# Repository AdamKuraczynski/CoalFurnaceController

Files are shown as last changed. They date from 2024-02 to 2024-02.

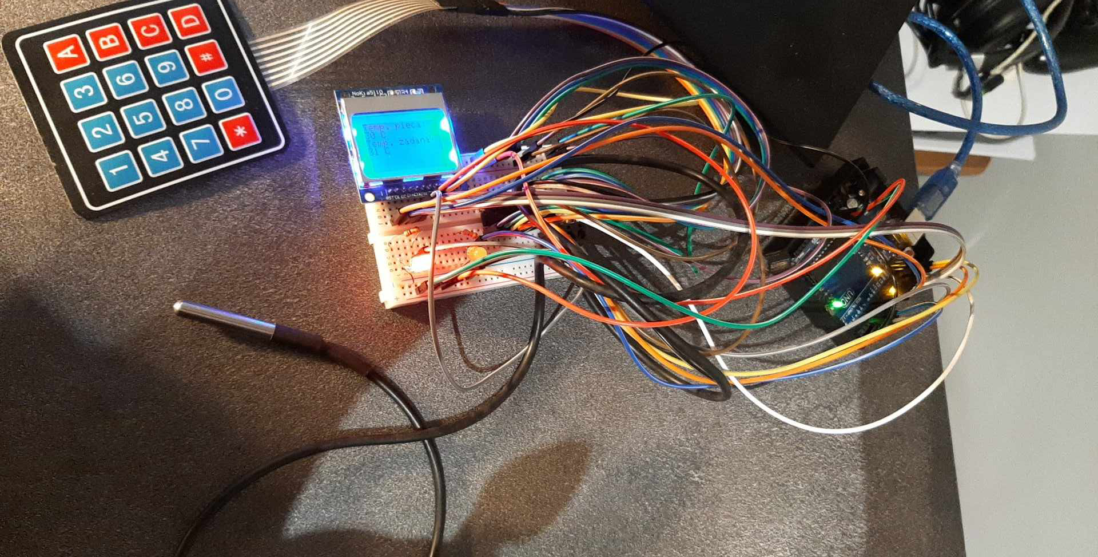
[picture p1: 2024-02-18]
DOC/SPR/IRL Project.png

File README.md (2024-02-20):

# CoalFurnaceController

This project utilizes an Arduino UNO R3 microcontroller as its base to control the pump and blower of a coal furnace. The repository includes all essential files and documents, detailing every step necessary for you to build it yourself.

#### Repository structure:
\PPT - This directory contains the presentation of the project in its initial, intermediate, and final stages. 

\SCH - This directory contains the complete project in Fusion 360 (along with its backup files) with all necessary libraries. It also contains PNG files with schematic and PCB layers.  

\SRC - This directory contains the source code, along with the necessary libraries required for compilation.  

\DOC\SPR - The directory contains all necessary documentation files for the project.  

## Other notes:

##### Hardware:  
Arduino UNO R3  
Breadboard 30  
USB B Cable  
Self-adhesive membrane keyboard 4x4 - 16 keys  
Temperature sensor DS18B20  
Diodes x 2  
Resistors 2x 330 Ohms, 1x 4.7 kOhms  
Pin Expander - Pcf8574 - I2C bus  
84x48 Nokia 5110 3310 display (pcd8544)  

##### Theory:
https://www.elektroda.pl/rtvforum/topic3668747.html   
https://forbot.pl/blog/kurs-elektroniki-prawa-ohma-i-kirchhoffa-id3986  

##### Schematic notes:
Project scanner I2C - checking ports ADDRESS 0x20  
(5-1.7) / 0.01 = 330 Ohms i.e., circuit power - V diode / diode operating range 0.005 to 0.02 = resistor value

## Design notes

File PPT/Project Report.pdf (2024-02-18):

| Instytut Informatyki Politechniki Śląskiej Zespół Mikroinformatyki i Teorii Automatów Cyfrowych
Rok akademicki | Rodzaj studiów*: SSI/NSI/NSM | Przedmiot: (Języki Asemblerowe/SMIW) | Grupa | Sekcja
2023/2024 | NSI | SMIW | 2 | 1
Prowadzący przedmiot: | Dr inż. Gabriel Drabik | | Termin: (dzień tygodnia, godzina)
Imię: Nazwisko: Email: | Adam Kuraczyński ak301824@student.polsl.pl | | Sobota
11:45

## Raport końcowy

Temat projektu:

Sterowanie procesem spalania w piecu węglowym

### Spis treści:

1. Temat projektu, opis założeń, opis funkcji urządzenia
2. Analiza zadania, lista potrzebnych elementów do zbudowania projektu, kosztorys
3. Specyfikacja wewnętrzna urządzenia
1) Schemat blokowy i ideowy urządzenia
2) Opis funkcji poszczególnych bloków układu
3) Schemat montażowy obejmujący projekt płytki drukowanej, rozmieszczenie elementów na płytce
4) Algorytm oprogramowania urządzenia (schemat blokowy)
5) Opis wszystkich zmiennych
6) Opis funkcji procedur
7) Opis integracji oprogramowania z układem elektronicznym
8) Szczegółowy opis działania ważniejszych procedur
4. Specyfikacja zewnętrzna urządzenia
1) Opis funkcji elementów sterujących urządzeniem
2) Opis funkcji elementów wykonawczych
3) Opis reakcji oprogramowania na zdarzenia zewnętrzne
4) Skrócona instrukcja obsługi urządzenia
5. Opis montażu układu, sposobu uruchamiania oraz testowania
1) Problemy, które wystąpiły w trakcie montażu, uruchomienia i ich rozwiązania
2) Testy poprawności działania urządzenia
6. Wnioski końcowe

1. Temat projektu, opis założeń, opis funkcji urządzenia

Tematem projektu jest stworzenie układu zarządzającego sterowaniem piecykiem węglowym starego typu. Taki układ po podłączeniu do prądu powinien mieć możliwość zmiany wartości zadanych w trakcie działania układu oraz wyświetlać aktualnie zadane parametry. Na podstawie zadanych parametrów układ powinien sterować pompą i dmuchawą pieca.

2. Analiza zadania, lista potrzebnych elementów do zbudowania projektu, kosztorys
Wymagane elementy do zbudowania projektu to następująco:
- Zasilanie
- Mikrokontroler
- Wyświetlacz LCD
- Klawiatura
- Czujnik temperatury

Analiza i wybór elementów:
- Mikrokontroler – zdecydowałem się na wybór Arudino Uno R3, gdyż korzystałem już tego urządzenia. Arduino obsługuje prace pod napięciem 5V i pozwala na zasilanie elementów napięciem 3.3V. Obsługuje wymagane I²C, jest kompatybilne z dużą ilością sprzętu i posiada wiele bibliotek.

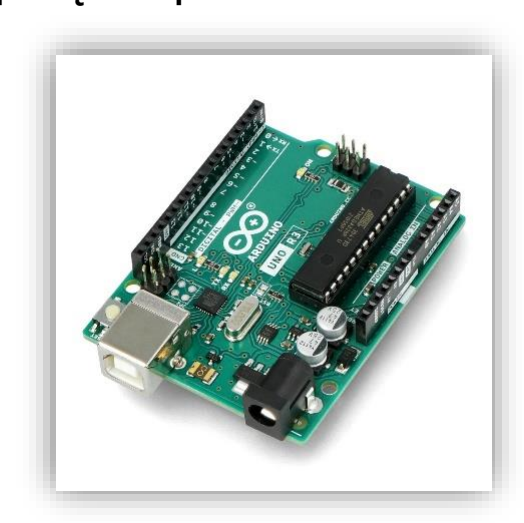
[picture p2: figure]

- Wyświetlacz LCD – zdecydowałem się na 84x48 nokia 5110 3310 (pcd8544). Wyświetlacz jest kompatybilny z Arduino Uno, jest stosunkowo tanim rozwiązaniem, pozwala na wyświetlanie informacji w wielu wierszach co pozwala na wyświetlenie intuicyjnych ekranów. Z powodu prostoty rozwiązania nie zdecydowałem się na wyświetlacz 2x16 HD44780 – nie wprowadza on niczego do projektu. Pracuje pod napięciem 3.3 V co pozwala na podłączenie do Arudino.

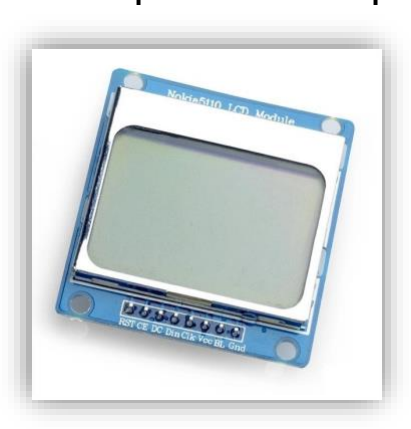
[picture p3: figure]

- Klawiatura – zdecydowałem się na klawiaturę membranowa 4x4 z powodu prostej obsługi z Arduino, dużej ilości
przycisków, | które | będą | potrzebne | do | potencjalnych
dodatkowych funkcjonalności systemu, prostoty działania i niskiego kosztu.

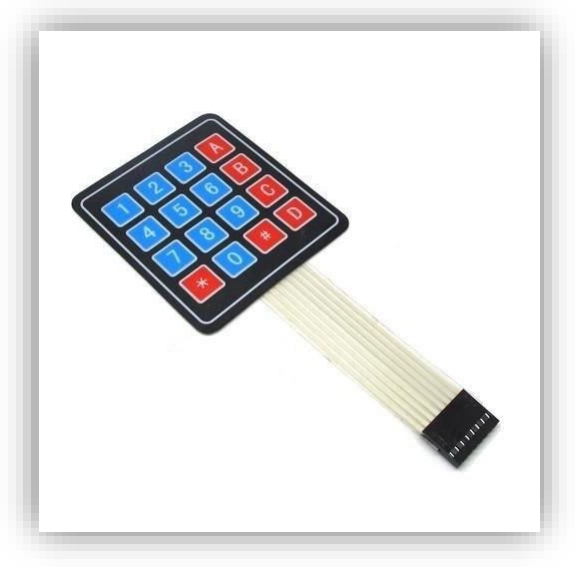
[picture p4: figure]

- Czujnik temperatury – zdecydowałem się na model DS18B20 z powodu bibliotek dostępnych do Arduino, dodatkowego
zabezpieczenia | wodoodpornego, | długiego | kabla
pozwalającego odseparowanie czujnika od reszty elementów, które z pewnością nie chcemy blisko wysokich temperatur.

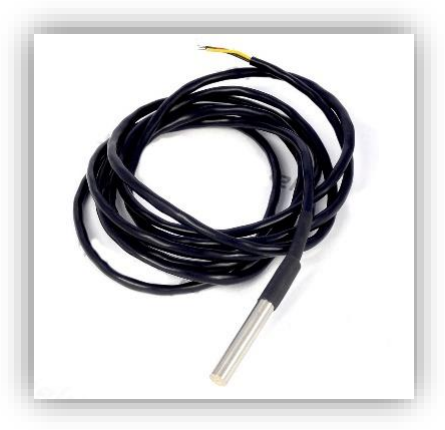
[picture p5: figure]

- Zasilanie układu – zdecydowałem się na zasilanie za pomocą kabla USB typ B z powodu prostej dostępności, możliwości wpięcia do komputera jak i gniazdka używając adaptera. Zasilanie dostarcza wystarczające napięcie do zasilenia Arduino. Jest to również tańsze rozwiązanie w porównaniu do osobnego zasilacza.

Kosztorys:

Rzecz | Sztuk | Koszt
Arduino UNO R3 | 1 | 120
Płytka stykowa 30 | 1 | 7
Kabel USB B | 1 | 20
Klawiatura membranowa samoprzylepna 4x4 - 16 klawiszy | 1 | 5
Czujnik temperatury DS18B20 | 1 | 18
Dioda LED | 2 | 3
Rezystor 330 Om | 2 | 2
Rezystor 4,7k Om | 1 | 2
Ekspander wprowadzeń Pcf8574 | 1 | 15
84 48 Nokia 5110 3310 wyświetlacz (pcd8544) | 1 | 25
Przewody połączeniowe męsko-męskie | 40 | 20
| Suma: | 237

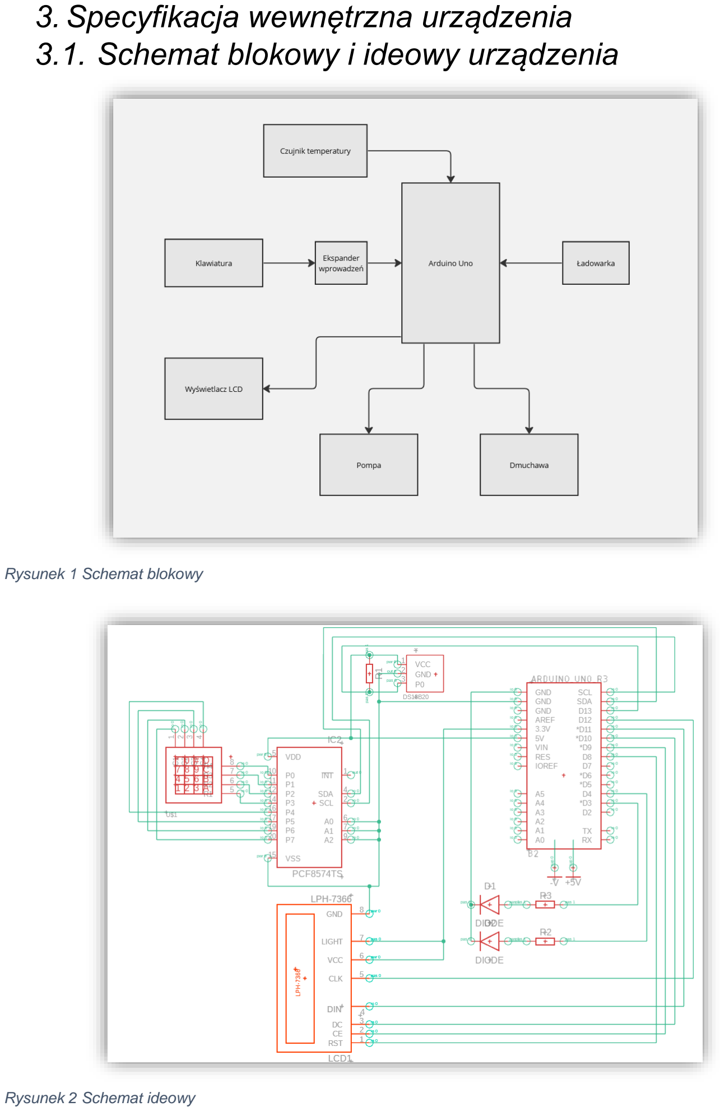
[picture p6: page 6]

3. Specyfikacja wewnętrzna urządzenia
3.1. Schemat blokowy i ideowy urządzenia

Rysunek 1 Schemat blokowy

Rysunek 2 Schemat ideowy

3.2. Opis funkcji poszczególnych bloków układu

Podłączenie klawiatury do ekspandera wprowadzeń – służy do interakcji użytkownika z systemem. Ekspander jest interfejsem w komunikacji klawiatura <-> Arduino.

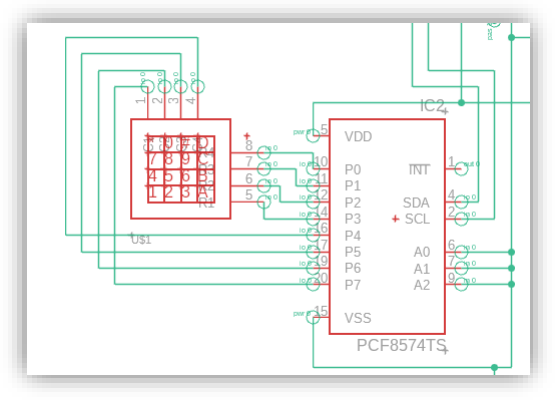
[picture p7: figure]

Podłączenie czujnika temperatury z mikrokontrolerem – służy do stałego odczytu temperatury. Używa protokołu OneWire.

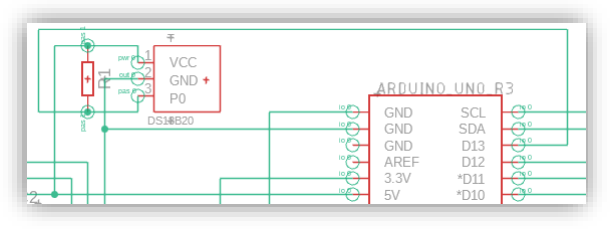
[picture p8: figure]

Podłączenie diod do mikrokontrolera – diody symbolizują pompę i dmuchawę, których włączaniem/wyłączaniem steruje Arduino.

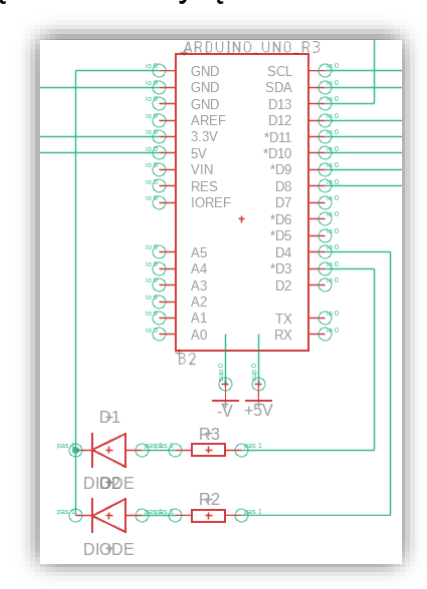
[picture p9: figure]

Podłączenie wyświetlacza – Arduino wysyła dane w celu wyświetlenia ich użytkownikowi. Wyświetlacz używa protokołu SPI.

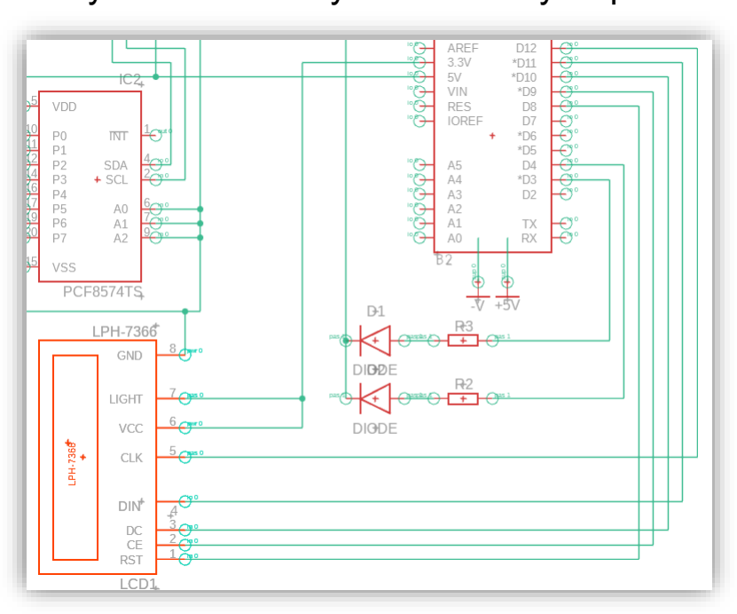
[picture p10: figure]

Podłączenie ekspandera wprowadzeń do mikrokontrolera – ekspander służy jako interfejs między klawiaturą a Arduino, dzięki niemu jest możliwość podpięcia większej ilości pinów cyfrowych. Komunikacja zachodzi przez magistrale I²C.

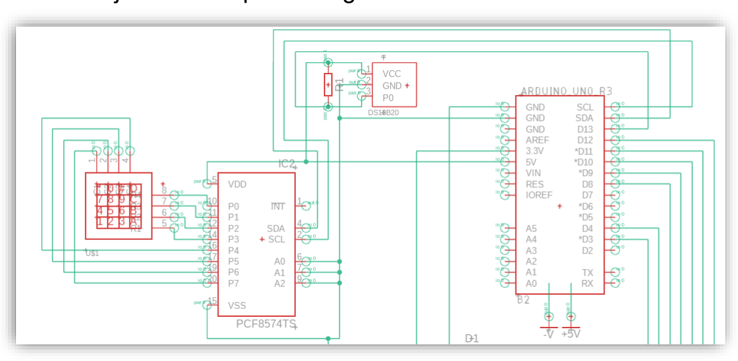
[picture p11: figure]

3.3. Schemat montażowy obejmujący projekt płytki drukowanej, rozmieszczenie elementów na płytce
B2 | ARDUINO _UNO_R3 | ARDUINO_UNO_R3 _SHIELDUNO_R3_S HIELD_NOLABELS_L OCK | UNO_R3_SHIELD_NO LABELS_LOCK | Arduino R3 Shield Footprint
D1 | DIODE | DIODEDO-214AB(SMC) | DIOM7959X625N | Diode Rectifier -Generic | Diode | Rectifier | DIODE
D2 | DIODE | DIODEDO-214AB(SMC) | DIOM7959X625N | Diode Rectifier -Generic | Diode | Rectifier | DIODE
IC2 | PCF8574TS | PCF8574TS | SSOP20 | I2C-Bus Remote 8-bit I/O expander
LCD1 | LPH-7366 | LPH-7366 | LPH-7366
R1 | | R_AXIAL-7.2MM-PITCH | RESAD724W46L381D 178B | Resistor Fixed -Generic | Resistor | Fixed
R2 | | R_AXIAL-7.2MM-PITCH | RESAD724W46L381D 178B | Resistor Fixed -Generic | Resistor | Fixed
R3 | | R_AXIAL-7.2MM-PITCH | RESAD724W46L381D 178B | Resistor Fixed - Generic Resistor | | Fixed
T | DS18B20 | A1324LLHLT-TLH | SOT95P285X113-3N | SENSOR HALL EFFECT ANALOG SOT23W | Sensor | Magnetic | A1324 LLHLT
U$1 | | KEYPAD4X4 | KEYPAD4X4

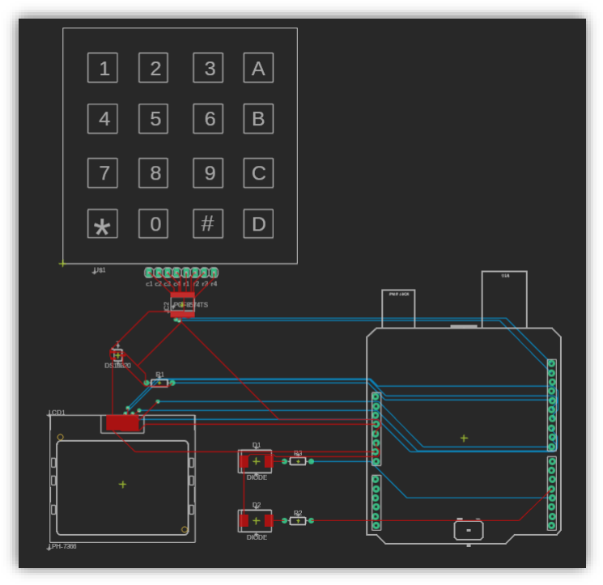
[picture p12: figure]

Rysunek 3 Projekt Płytki

3.4. Algorytm oprogramowania urządzenia (schemat blokowy)

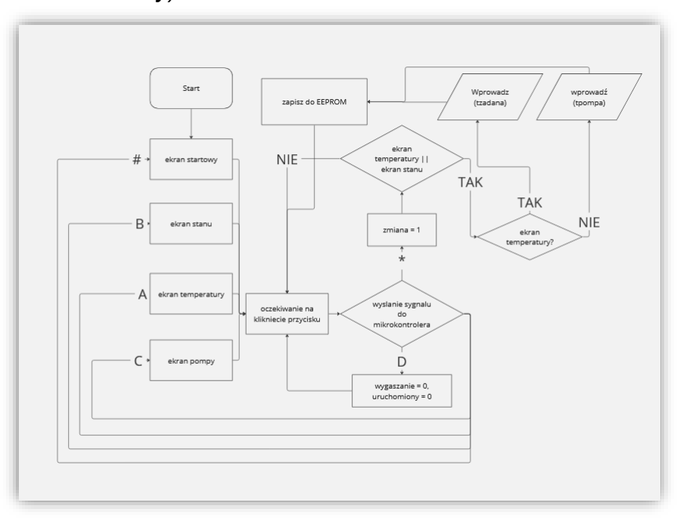
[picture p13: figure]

Rysunek 4 Algorytm blokowy

3.5. Opis wszystkich zmiennych
#define ONE_WIRE_BUS 13 | - zmienna z adresem czujnika temperatury

OneWire oneWire(ONE_WIRE_BUS); | - zmienna tworzaca komunikacje OneWire
DallasTemperature sensors(&oneWire); | - zmienna tworzaca komunikacje DallasTemperature uzywając OneWire
Adafruit_PCD8544 display =
Adafruit_PCD8544(12, 11, 10, 9, 8); | - zmienna tworząca komunikacje z wyswietlaczem
const byte pompa = 3; | - zmienna z adresem pompy
const byte dmuchawa = 4; | - zmienna z adresem dmuchawy
int tzadana = 29; | - zmienna z wartością, do której działa dmuchawa
int tpompa = 27; | - zmienna z wartością temperatury, od której właczana jest pompa
int temperatura; | - zmienna z wartością aktualnej temperatury

byte ekran = 0; | - zmienna pomocnicza do przejść między ekranami
byte zmiana = 0; | - zmienna sygnalizujaca wejście do Trybu Edycji
byte uruchomiony=0; | - zmienna sygnalizujaca uruchomienie Pompy
byte wygaszanie=0; | - zmienna sygnalizująca skończenie 1 cyklu działania układu
const byte ROWS = 4; | - zmienna pomocnicza z ilościa wierszy
const byte COLS = 4; | - zmienna pomocnicza z ilościa kolumn
Char keys[ROWS][COLS] = {
{'1','2','3','A'},
{'4','5','6','B'},
{'7','8','9','C'},
{'*','0','#','D'} };
- zmienna pomocnicza mapująca wartości klawiszy
byte rowPins[ROWS] = {0, 1, 2, 3}; | - zmienna pomocnicza z adresami wierszy klawiatury
byte colPins[COLS] = {4, 5, 6, 7}; | - zmienna pomocnicza z adresami kolumn klawiatury
int i2caddress = 0x20; | - zmienna pomocnicza z adresem i2c ekspandera wprowadzeń
Keypad_I2C kpd = Keypad_I2C(
makeKeymap(keys), rowPins, colPins,
ROWS, COLS, i2caddress );
- zmienna tworząca komunikacje klawiatury

temperatura=sensors.getTempCByIndex(0); - zmienna do przechowywania temperatury odebranej przes czujnik
char klawisz = kpd.getKey(); | - zmienna do przechowywania ostatniego wciśniętego przycisku
3.6. Opis funkcji procedur
int odczytLiczba() | - funkcja, która zwraca zmieniona wartość temperatury
int odczytCyfra() | - funkcja, która odczytuje cyfry z klawiatury w celu zmiany temperatury zadanej
void EkranStartowy() | - funkcja inicjująca ekran startowy
void EkranTemperatury () | - funkcja inicjująca ekran temperatury
void EkranStanu() | - funkcja inicjująca ekran stanu
void EkranPompa() | - funkcja inicjująca ekran pompy
void setup() | - funkcja ustawiająca interfejsy do obsługi
void loop() | - główna funkcja mikrokontrolera, zarządza zmianami ekranów i zachowaniem pompy i dmuchawy
switch (klawisz) | - przełącznik obsługujący zmiane ekranów
switch (ekran) | - przełącznik obsługujący zmiane ekranów
display.clearDisplay(); | - czyści ekran
display.setTextSize(1); | - zmienia wielkość czcionki na ekranie
display.setTextColor(BLACK); | - zmienia kolor czcionki na ekranie
display.setCursor(0, 0); | - ustawia pozycje kursora

display.print(); | - drukuje tekst do ekranu
display.println(); | - przechodzi do nowej linii na ekranie
display.display(); | - wyświetla cały kontekst na ekranie
display.begin(); | - inicializuje ekran
display.setContrast(60); | - zmienia kontrast ekranu
Serial.begin(9600); | - rozpoczyna komunikacje seryjną
sensors.begin(); | - inicializuje czujniki temperatury
Wire.begin(); | - inicializuje komunikacje I2C
kpd.begin(); | - inicializuje klawiature
pinMode(pompa, OUTPUT); | - konfiguruje pin jako wyjście
pinMode(dmuchawa, OUTPUT); - konfiguruje pin jako wyjście
EEPROM.put(100, tzadana); | - wpisuje wartość tzadana do EEPROM na adresie 100
EEPROM.get(100, tzadana); | - odczytuje wartość tzadana z EEPROM z adresu 100
sensors.requestTemperatures(); - inicialuzje pomiary temperatury z sensora temperatury
sensors.getTempCByIndex(i); | - odczytuje wartość temperatury z sensora
digitalWrite(dmuchawa,HIGH); | - ustawia pin dmuchawa jako 1
digitalWrite(dmuchawa,LOW); | - ustawia pin dmuchawa jako 0
digitalWrite(pompa,HIGH); | - ustawia pin pompa jako 1
digitalWrite(pompa,LOW); | - ustawia pin pompa jako 0
3.7. Opis | integracji | oprogramowania | z | układem
elektronicznym

Oprogramowanie wykorzystuje następne biblioteki:

- Adafruit_GFX oraz Adafruit_PCD8544 – wykorzystane w celu zapewnienia komunikacji z wyświetlaczem NOKIA typu PCD8544,
- Keypad_I2C - wykorzystana do zapewnienia komunikacji z klawiaturą, użyta została Keypad_I2C a nie Keypad jako że komunikacja zachodzi poprzez ekspander wprowadzeń I2C,
- Wire, OneWire, DallasTemperature - wykorzystane, aby zapewnić komunikację z czujnikiem temperatury,
- EEPROM - wykorzystana, aby wartości zadane dla pompy oraz dmuchawy były zachowane między włączeniami systemu.

3.8. Szczegółowy opis działania ważniejszych procedur

Gdy aktualnie odczytana temperatura jest wyższa niż zadana dla systemu oraz jego tryb to wygaszanie to dmuchawa jest wyłączona. Jeśli nie to dmuchawa działa, jest to zabezpieczenie przed działaniem dmuchawy cały czas

if ((temperatura>=tzadana)||(wygaszanie==1)) digitalWrite(dmuchawa,LOW);
else digitalWrite(dmuchawa,HIGH);

Gdy aktualnie odczytana temperatura jest wyższa od temperatury zadanej dla pompy to pompa się uruchamia, a system przechodzi w tryb uruchomiony tj. grzeje dom.

if(temperatura>tpompa) {
digitalWrite(pompa,HIGH);
uruchomiony=1;
} else digitalWrite(pompa,LOW);

Gdy cykl został uruchomiony tj. pompa choć raz się włączyła oraz aktualny stan pompy to 0, czyli wyłączona to rozpoczyna się proces wygaszania mający na celu zabezpieczenie systemu przed działaniem dmuchawy cały czas.

if((uruchomiony==1)&&(digitalRead(pompa)==0)) wygaszanie=1;

Zawsze pierwsza liczba wprowadzona w Trybie edycji to liczba dziesiątek a druga liczba jedności.

int odczytLiczba()
{
return odczytCyfra() * 10 + odczytCyfra(); }

4. Specyfikacja zewnętrzna urządzenia
4.1. Opis funkcji elementów sterujących urządzeniem

Sterowanie używając klawiatury:

- Przycisk „A” – przejście do Ekranu Temperatury
- Przycisk „B” – przejście do Ekranu Stanu
- Przycisk „C” – przejście do Ekranu Pompy
- Przycisk „#” – przejście do Ekranu Startowego
- Przycisk „D” – zresetowanie zmiennych i ponowne uruchomienie cyklu
- Przycisk „*” – przejście do Trybu Edycji temperatury na Ekranie Temperatury i Ekranie Pompy
- Przyciski 0-9 – w Trybie Edycji pozwalają na wybranie temperatury

Układ jest wyposażony w przycisk restartu pozwalający na restart mikrokontrolera.

4.2. Opis funkcji elementów wykonawczych

84 48 Nokia 5110 3310 Wyświetlacz LED (pcd8544) – wyświetla informacje o temperaturze i stanach pompy i dmuchawy oraz zadanych wartościach
Dioda czerwona – symbolizuje uruchomienie pompy pieca węglowego Dioda żółta – symbolizuje uruchomienie dmuchawy pieca węglowego Czujnik temperatury DS18B20 – odczytuje temperaturę

4.3. Opis | reakcji | oprogramowania | na | zdarzenia
zewnętrzne

Wciśnięcie przycisku „A” – przejście do Ekranu Temperatury Wciśnięcie przycisku „B” – przejście do Ekranu Stanu Wciśnięcie przycisku „C” – przejście do Ekranu Pompy Wciśnięcie przycisku „#” – przejście do Ekranu Startowego Wciśnięcie przycisku „D” – zresetowanie zmiennych i ponowne uruchomienie cyklu
Wciśnięcie przycisku „*” – przejście do Trybu Edycji temperatury na Ekranie Temperatury i Ekranie Pompy
Wciśnięcie przycisków 0-9 – w Trybie Edycji pozwalają na wybranie temperatury
Wciśnięcie przycisku restartu na mikrokontrolerze – resetuje mikrokontroler a ekran wraca do Ekranu Startowego
Podłączenie i odłączenie źródła zasilania – uruchamia i wyłącza urządzenie
Czujnik temperatury – ogrzanie lub oziębienie czujnika zmienia działanie całego układu - włącza bądź wyłącza pompę i dmuchawę
4.4. Skrócona instrukcja obsługi urządzenia

Po podłączeniu urządzenia do prądu na wyświetlaczu pojawia się ekran startowy. Informuje nas o tym, że klikając na klawiaturze „A” przenosimy się do Ekranu Temperatury, klikając „B” do Ekranu Stanu a klikając „C” do Ekranu Pompy. Klikając „#” wracamy do ekranu startowego. Na ekranie temperatury otrzymujemy informacje o temperaturze pieca tj. aktualnej temperaturze zmierzonej przez czujnik temperatury oraz temperaturze zadanej to jest temperatury, która chcemy osiągnąć – temperatura, do której ma być uruchomiona dmuchawa. Ekran Stanu informuje nas o aktualnym stanie dmuchawy i pompy, czy są włączone czy nie.

Ekran Pompy informuje nas o temperaturze włączenia pompy. Klikając „*” na klawiaturze na Ekranie Temperatury jesteśmy w stanie zmienić zadana temperaturę dmuchawy, a na ekranie Pompy klikając „*” na klawiaturze jesteśmy w stanie zmienić temperaturę zadana pompy. Po zadaniu tych temperatur w standardowym przypadku dmuchawa powinna się włączyć, po tym pompa powinna się włączyć, następnie wyłącza się dmuchawa, a po tym pompa – dochodzi do resetu systemu. Po tym wystarczy, że na klawiaturze wciśniemy „D” aby zresetować system – dmuchawa znowu zacznie działać. To zabezpiecza system przed działaniem cały czas – nawet jak tego nie chcemy.

5. Opis montażu układu, sposobu uruchamiania oraz testowania

Układ został podłączony używając płytki prototypowej. Na płytce umieszczone zostały diody, rezystory, wyświetlacz, czujnik temperatury oraz ekspander wprowadzeń. Następnie używając przewodów połączeniowych wszystko zostało ze sobą połączone i osobno przetestowane w kolejności czujnik temperatury, diody i rezystory, wyświetlacz, klawiatura i ekspander wprowadzeń. Po podłączeniu wszystkiego wykonane zostało oprogramowanie, które testuje każde z urządzeń.

5.1. Problemy, które wystąpiły w trakcie montażu, uruchomienia i ich rozwiązania

W trakcie testowania urządzenia z przyczyn mi nieznanych wyświetlacz LCD przestał działać, zmuszony byłem do zakupu nowego egzemplarza.

5.2. Testy poprawności działania urządzenia

Testy opierały się na sprawdzeniu pełnej funkcjonalności urządzenia: działanie klawiatury, wyświetlacza, bieżący pomiar temperatury, jak reagują pompa i dmuchawa na odmierzone temperatury oraz czy układ działa po podłączeniu do zasilania. Wszystkie testy przeszły pomyślnie.

6. Wnioski końcowe

Układ sprawdza się, jeśli chodzi o podstawowe wymogi. Można jednak go rozbudować o dodatkowe funkcjonalności:

- Zamknąć go w obudowie, aby zabezpieczyć elementy,
- Odczytanie temperatury mogłoby zostać wykonywane w części mieszkalnej budynku a informacja o temperaturze przekazywana do głównego kontrolera,
- Można | usprawnić | wyświetlanie | komunikatów | na
wyświetlaczu, aby wszystko odbywało się na jednej stronie bez wymogu zmiany ekranów wyświetlania.

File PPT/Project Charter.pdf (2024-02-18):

Data | Ocena:

Założenia:

Prezentacja:

Implementacja

Raport

Ocena końcowa:

Data | Obecność | Uwagi
| Instytut Informatyki Politechniki Śląskiej Zespół Mikroinformatyki i Teorii Automatów Cyfrowych
Rok akademicki | Rodzaj studiów*: SSI/NSI/NSM | Przedmiot: (Języki Asemblerowe/SMIW) | Grupa | Sekcja
2023/2024 | NSI | SMIW | 2 | 1
Prowadzący przedmiot: | Dr inż. Gabriel Drabik | | Termin: (dzień tygodnia, godzina)
Imię: Nazwisko: Email: | Adam Kuraczyński ak301824@student.polsl.pl | | Sobota
11:45

## Karta projektu

Temat projektu:

Sterowanie procesem spalania w piecu węglowym

Główne założenia projektu:
Układ ma na celu zautomatyzowanie procesu spalania w piecyku węglowym starego typu. Do płytki Arduino UNO R3 podłączone są następujące elementy: wyświetlacz graficzny 84x48 LCD NOKIA 5110/3310, czujnik temperatury, klawiatura membranowa 4x4, dmuchawa i pompa pieca (ich podpięcie zasymuluje poprzez użycie diod). Z powodu braku wystarczającej ilości pinów na płytce do podpięcia klawiatury użyty zostanie ekspander wprowadzeń magistrali I2C 8-bitowy Pcf8574.

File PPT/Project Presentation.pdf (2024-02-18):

## Sterowanie procesem spalania w piecu węglowym

Adam Kuraczyński

# Założenie

- Umożliwienie sterowania procesu spalania w piecyku
węglowym starego typu
- Możliwość zmiany wartości zadanych w trakcie działania układu – bez potrzeby jego wyłączania

# Elementy układu

- Moduł Arduino UNO R3,
- Wyświetlacz graficzny 84x48 LCD NOKIA 5110/3310,
- Czujnik temperatury DS18B20,
- Klawiatura membranowa 4x4,
- Dmuchawa i pompa pieca (ich podpięcie zasymuluje poprzez użycie żółtej i czerwonej diody)
- Ekspander wyprowadzeń I²C 8-bitowy PCF8574,
- Rezystor 4.6 kΩ,
- Rezystor 330 Ω x 2,

# Sposób działania

- Sterowanie układem przez użytkownika zachodzi poprzez interfejs I²C
- Komunikacja z wyświetlaczem odbywa się poprzez interfejs SPI (Serial Peripheral Interface)
- Status pracy urządzenia, odczytane wartości oraz informacje zwrotne wyświetlane są na ekranie LCD
- Układ zasilany jest napięciem 5V (USB 2.0)

# Schemat ideowy układu

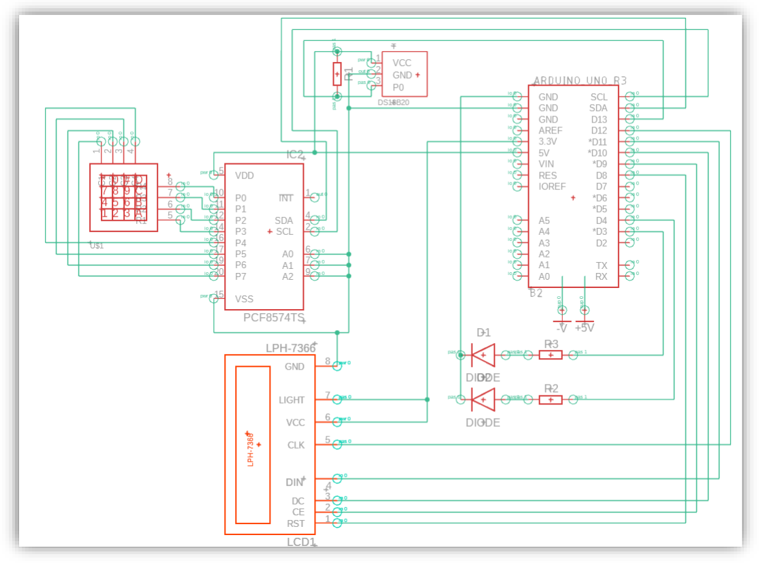
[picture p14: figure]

# Aktualny stan prac

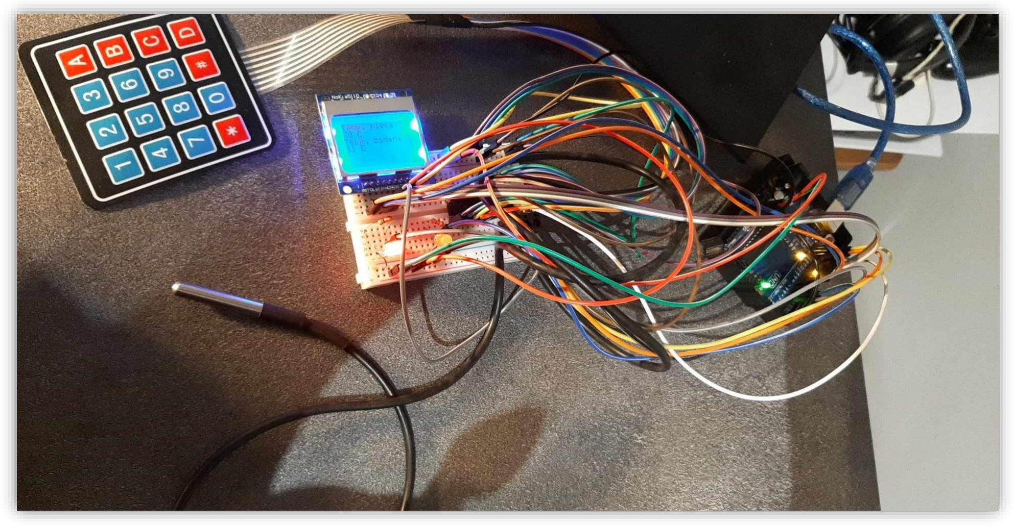
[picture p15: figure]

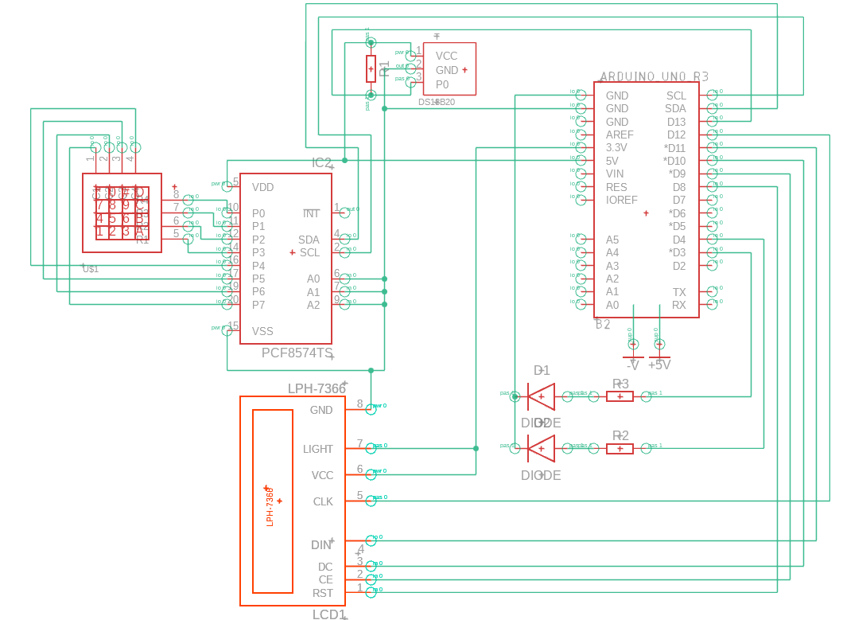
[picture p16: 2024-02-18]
SCH/Circuit Schematic.png

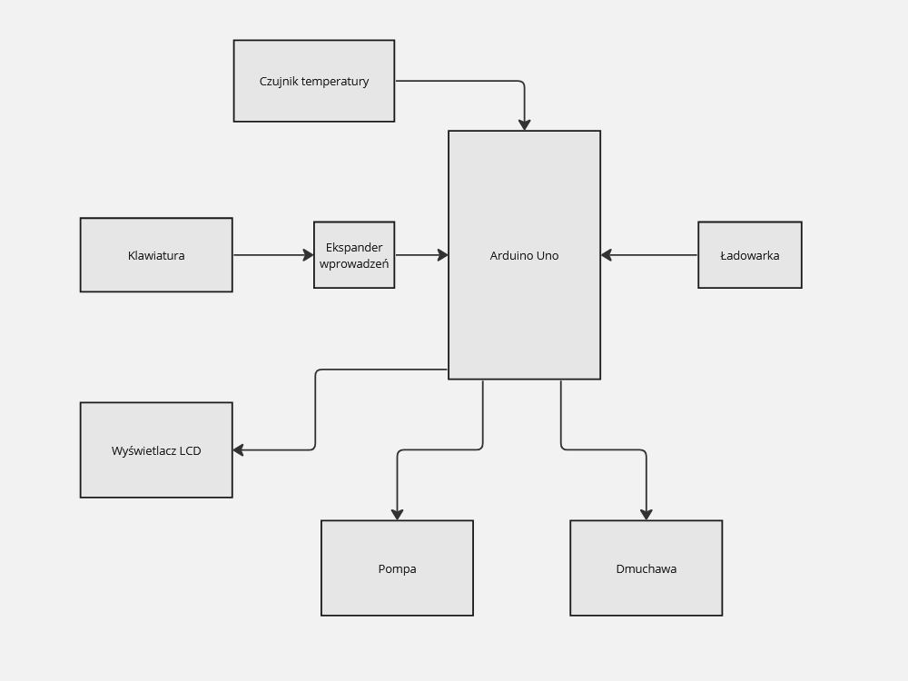
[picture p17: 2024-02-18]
DOC/SPR/Block Diagram.png

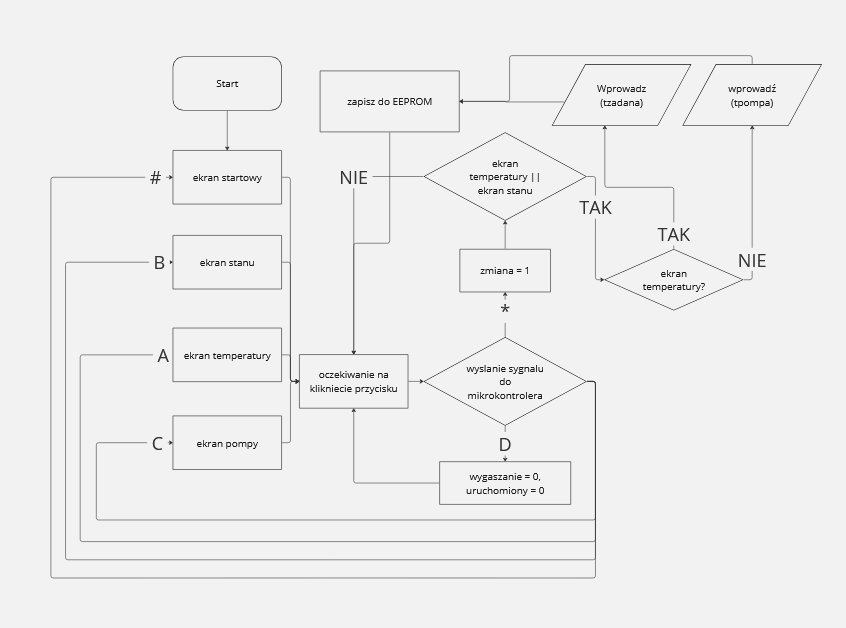
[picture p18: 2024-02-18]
DOC/SPR/Algorithm Block Diagram.png

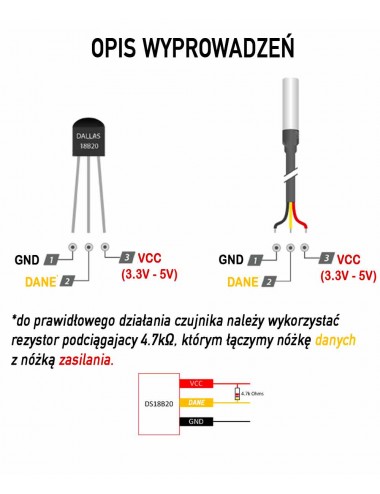
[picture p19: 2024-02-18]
DOC/SPR/TemperatureSensorDS18B20.png

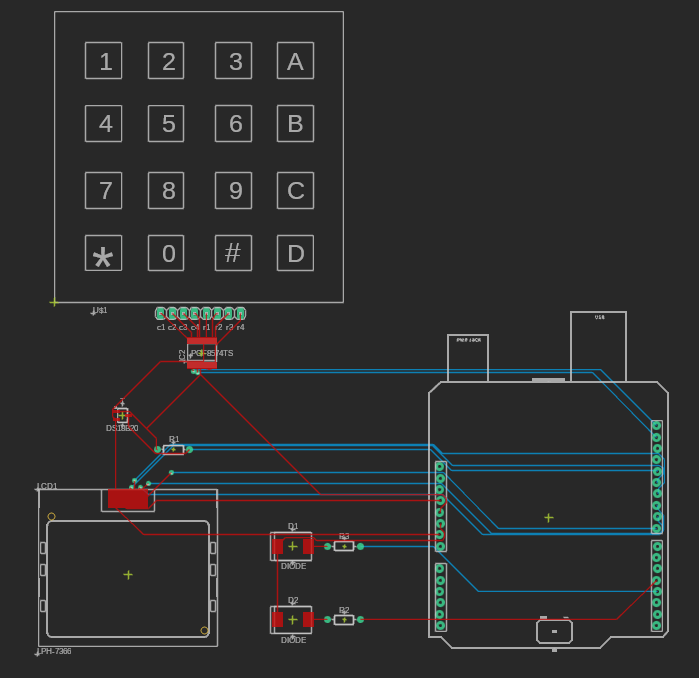
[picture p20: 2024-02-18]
SCH/PCB Board.png

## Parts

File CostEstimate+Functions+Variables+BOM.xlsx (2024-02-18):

#define ONE_WIRE_BUS 13 | - | zmienna z adresem czujnika temperatury | Rzecz | Sztuk | Koszt | Part | Value | Device | Package | Description | CAT | SUB-CAT | VALUE
OneWire oneWire(ONE_WIRE_BUS); | - | zmienna tworzaca komunikacje OneWire | Arduino UNO R3 | 1 | 120 | B2 | ARDUINO_UNO_R3 | ARDUINO_UNO_R3_SHIELDUNO_R3_SHIELD_NOLABELS_LOCK | UNO_R3_SHIELD_NOLABELS_LOCK | Arduino R3 Shield Footprint
DallasTemperature sensors(&oneWire); | - | zmienna tworzaca komunikacje DallasTemperature uzywając OneWire | Płytka stykowa 30 | 1 | 7 | D1 | DIODE | DIODEDO-214AB(SMC) | DIOM7959X625N | Diode Rectifier - Generic | Diode | Rectifier | DIODE
Adafruit_PCD8544 display = Adafruit_PCD8544(12, 11, 10, 9, 8); | - | zmienna tworząca komunikacje z wyswietlaczem | Kabel USB B | 1 | 20 | D2 | DIODE | DIODEDO-214AB(SMC) | DIOM7959X625N | Diode Rectifier - Generic | Diode | Rectifier | DIODE
const byte pompa = 3; | - | zmienna z adresem pompy | Klawiatura membranowa samoprzylepna 4x4 - 16 klawiszy | 1 | 5 | IC2 | PCF8574TS | PCF8574TS | SSOP20 | I2C-Bus Remote 8-bit I/O expander
const byte dmuchawa = 4; | - | zmienna z adresem dmuchawy | Czujnik temperatury DS18B20 | 1 | 18 | LCD1 | LPH-7366 | LPH-7366 | LPH-7366
int tzadana = 29; | - | zmienna z wartością do której działa dmuchawa | Dioda LED | 2 | 3 | R1 |  | R_AXIAL-7.2MM-PITCH | RESAD724W46L381D178B | Resistor Fixed - Generic | Resistor | Fixed
int tpompa = 27; | - | zmienna z wartością temperatury od której właczana jest pompa | Rezystor 330 Om | 2 | 2 | R2 |  | R_AXIAL-7.2MM-PITCH | RESAD724W46L381D178B | Resistor Fixed - Generic | Resistor | Fixed
int temperatura; | - | zmienna z wartością aktualnej temperatury | Rezystor 4,7k Om | 1 | 2 | R3 |  | R_AXIAL-7.2MM-PITCH | RESAD724W46L381D178B | Resistor Fixed - Generic | Resistor | Fixed
byte ekran = 0; | - | zmienna pomocnicza do przejść między ekranami | Ekspander wprowadzeń Pcf8574 | 1 | 15 | T | DS18B20 | A1324LLHLT-TLH | SOT95P285X113-3N | SENSOR HALL EFFECT ANALOG SOT23W | Sensor | Magnetic | A1324LLHLT
byte zmiana = 0; | - | zmienna sygnalizujaca wejście do Trybu Edycji | 84 48 Nokia 5110 3310 wyświetlacz (pcd8544) | 1 | 25 | U$1 |  | KEYPAD4X4 | KEYPAD4X4
byte uruchomiony=0; | - | zmienna sygnalizujaca uruchomienie Pompy | Przewody połączeniowe męsko-męskie | 40 | 20
byte wygaszanie=0; | - | zmienna sygnalizująca skończenie 1 cyklu działania układu |  | Suma: | 237
const byte ROWS = 4; | - | zmienna pomocnicza z ilościa wierszy
const byte COLS = 4; | - | zmienna pomocnicza z ilościa kolumn
char keys[ROWS][COLS] = { {'1', '2', '3', 'A'}, {'4', '5', '6', 'B'}, {'7', '8', '9', 'C'}, {'*', '0', '#', 'D'} }; | - | zmienna pomocnicza mapująca wartości klawiszy
byte rowPins[ROWS] = {0, 1, 2, 3}; | - | zmienna pomocnicza z adresami wierszy klawiatury
byte colPins[COLS] = {4, 5, 6, 7}; | - | zmienna pomocnicza z adresami kolumn klawiatury
int i2caddress = 0x20; | - | zmienna pomocnicza z adresem i2c ekspandera wprowadzeń
Keypad_I2C kpd = Keypad_I2C( makeKeymap(keys), rowPins, colPins, ROWS, COLS, i2caddress ); | - | zmienna tworząca komunikacje klawiatury
temperatura=sensors.getTempCByIndex(0); | - | zmienna do przechowywania temperatury odebranej przes czujnik
char klawisz = kpd.getKey(); | - | zmienna do przechowywania ostatniego wciśniętego przycisku
int odczytLiczba() | - | funkcja która zwraca zmieniona wartość temperatury
int odczytCyfra() | - | funkcja która odczytuje cyfry z klawiatury w celu zmiany temperatury zadanej
void EkranStartowy() | - | funkcja inicjująca ekran startowy
void EkranTemperatury () | - | funkcja inicjująca ekran temperatury
void EkranStanu() | - | funkcja inicjująca ekran stanu
void EkranPompa() | - | funkcja inicjująca ekran pompy
void setup() | - | funkcja ustawiająca interfejsy do obsługi
void loop() | - | główna funkcja mikrokontrolera, zarządza zmianami ekranów i zachowaniem pompy i dmuchawy
switch (klawisz) | - | przełącznik obsługujący zmiane ekranów
switch (ekran) | - | przełącznik obsługujący zmiane ekranów
display.clearDisplay(); | - | czyści ekran
display.setTextSize(1); | - | zmienia wielkość czcionki na ekranie
display.setTextColor(BLACK); | - | zmienia kolor czcionki na ekranie
display.setCursor(0, 0); | - | ustawia pozycje kursora
display.print(); | - | drukuje tekst do ekranu
display.println(); | - | przechodzi do nowej linii na ekranie
display.display(); | - | wyświetla cały kontekst na ekranie
display.begin(); | - | inicializuje ekran
display.setContrast(60); | - | zmienia kontrast ekranu
Serial.begin(9600); | - | rozpoczyna komunikacje seryjną
sensors.begin(); | - | inicializuje czujniki temperatury
Wire.begin(); | - | inicializuje komunikacje I2C
kpd.begin(); | - | inicializuje klawiature
pinMode(pompa, OUTPUT); | - | konfiguruje pin jako wyjście
pinMode(dmuchawa, OUTPUT); | - | konfiguruje pin jako wyjście
EEPROM.put(100, tzadana); | - | wpisuje wartość tzadana do EEPROM na adresie 100
EEPROM.get(100, tzadana); | - | odczytuje wartość tzadana z EEPROM z adresu 100
sensors.requestTemperatures(); | - | inicialuzje pomiary temperatury z sensora temperatury
sensors.getTempCByIndex(i); | - | odczytuje wartość temperatury z sensora
digitalWrite(dmuchawa,HIGH); | - | ustawia pin dmuchawa jako 1
digitalWrite(dmuchawa,LOW); | - | ustawia pin dmuchawa jako 0
digitalWrite(pompa,HIGH); | - | ustawia pin pompa jako 1
digitalWrite(pompa,LOW); | - | ustawia pin pompa jako 0

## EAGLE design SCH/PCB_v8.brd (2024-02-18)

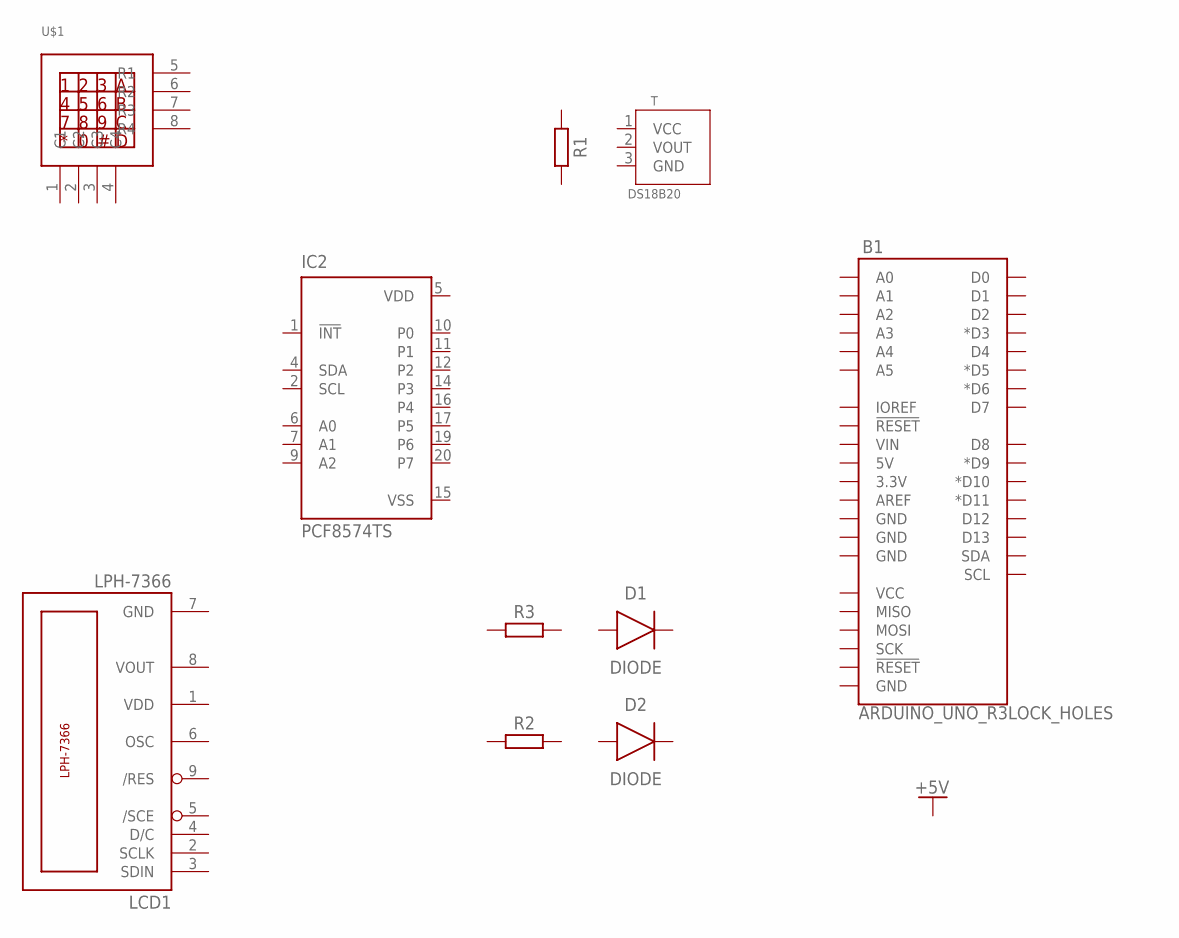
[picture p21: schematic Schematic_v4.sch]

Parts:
B1: ARDUINO_UNO_R3LOCK_HOLES; ARDUINO_R3_LOCK_HOLES
D1, D2: DIODE; DIOM7959X625N
IC2: PCF8574TS; SSOP20
LCD1: LPH-7366
R1, R2, R3: R_AXIAL-7.2MM-PITCH; RESAD724W46L381D178B
T: DS18B20; SOT95P285X113-3N; MPN DS18B20
U$1: KEYPAD4X4

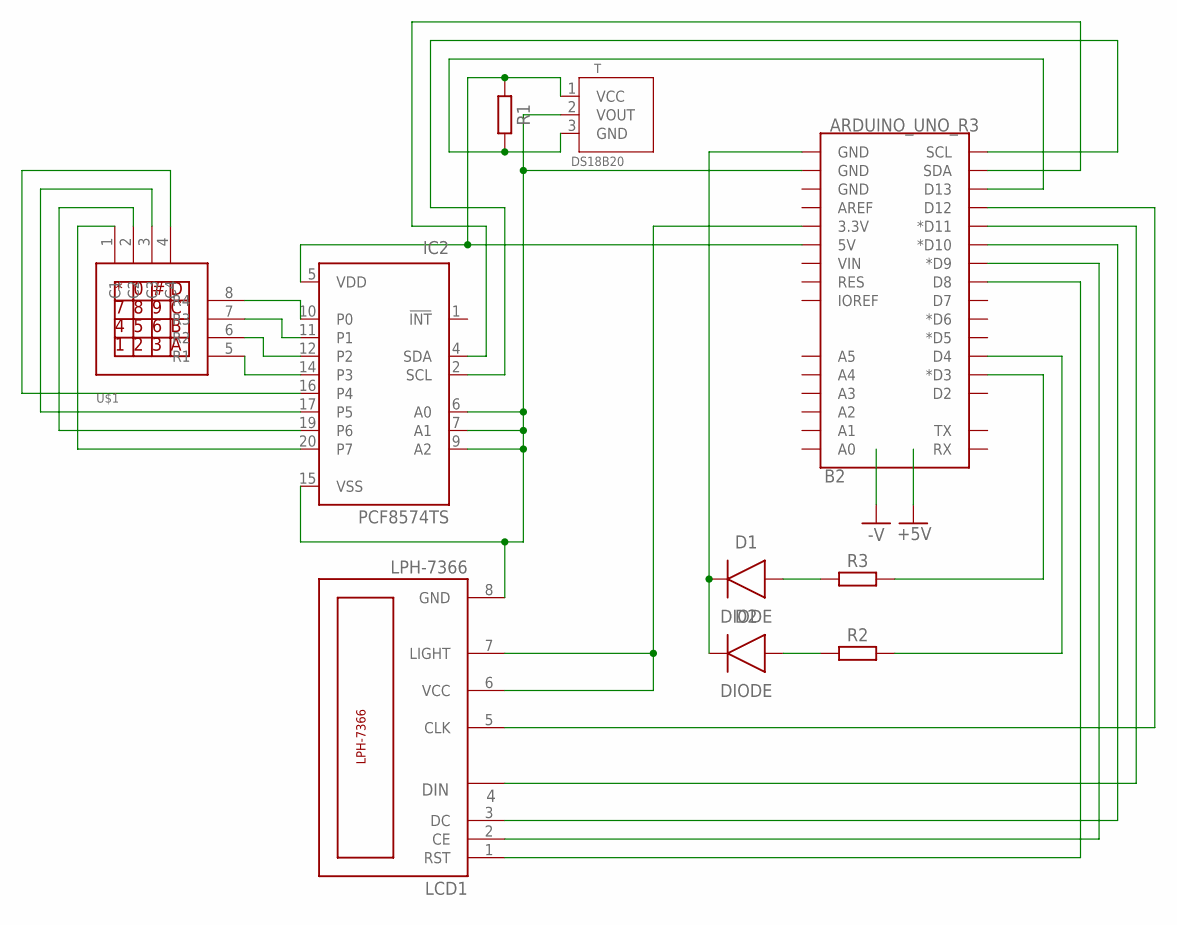
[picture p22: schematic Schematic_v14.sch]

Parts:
B2: ARDUINO_UNO_R3; UNO_R3_SHIELD_NOLABELS_LOCK
D1, D2: DIODE; DIOM7959X625N
IC2: PCF8574TS; SSOP20
LCD1: LPH-7366
R1, R2, R3: R_AXIAL-7.2MM-PITCH; RESAD724W46L381D178B
T: DS18B20; SOT95P285X113-3N; MPN DS18B20
U$1: KEYPAD4X4

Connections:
unnamed: B2.5V, IC2.5 (VDD), R1.1, T.1 (VCC)
unnamed: B2.D13, R1.2, T.3 (GND)
unnamed: D1.2 (A), R3.1
unnamed: B2.D3 (*D3), R3.2
unnamed: B2.D4, R2.2
unnamed: D2.2 (A), R2.1
unnamed: B2.GND@0 (GND), D1.1 (C), D2.1 (C)
unnamed: IC2.10 (P0), U$1.8 (R4)
unnamed: B2.GND@1 (GND), IC2.6 (A0), IC2.7 (A1), IC2.9 (A2), IC2.15 (VSS), LCD1.8 (GND), T.2 (VOUT)
unnamed: B2.SCL, IC2.2 (SCL)
unnamed: IC2.11 (P1), U$1.7 (R3)
unnamed: IC2.12 (P2), U$1.6 (R2)
unnamed: IC2.14 (P3), U$1.5 (R1)
unnamed: IC2.20 (P7), U$1.1 (C1)
unnamed: IC2.19 (P6), U$1.2 (C2)
unnamed: IC2.17 (P5), U$1.3 (C3)
unnamed: IC2.16 (P4), U$1.4 (C4)
unnamed: B2.SDA, IC2.4 (SDA)
unnamed: B2.D8, LCD1.1 (RST)
unnamed: B2.D9 (*D9), LCD1.2 (CE)
unnamed: B2.D10 (*D10), LCD1.3 (DC)
unnamed: B2.D11 (*D11), LCD1.4 (DIN)
unnamed: B2.D12, LCD1.5 (CLK)
unnamed: B2.3.3V, LCD1.6 (VCC), LCD1.7 (LIGHT)

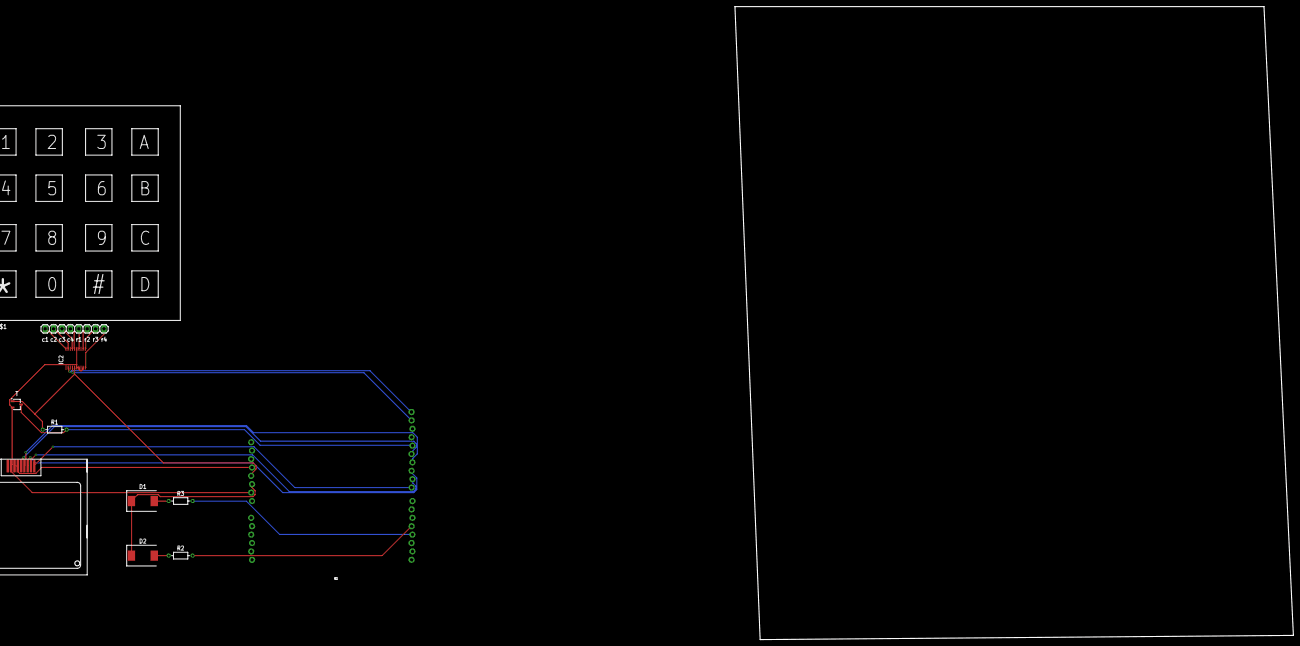
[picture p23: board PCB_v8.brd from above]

Board: 2 copper layers, 168.9 x 191.4 mm, 10 parts (0 on the bottom side), 24 nets.

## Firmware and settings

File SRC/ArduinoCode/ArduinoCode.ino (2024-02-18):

#include <Adafruit_GFX.h>
#include <Adafruit_PCD8544.h>
#include <Keypad_I2C.h>
#include <Keypad.h>
#include <Wire.h>
#include <OneWire.h>
#include <DallasTemperature.h>
#include <EEPROM.h>

#define ONE_WIRE_BUS 13

OneWire oneWire(ONE_WIRE_BUS);
DallasTemperature sensors(&oneWire);

Adafruit_PCD8544 display = Adafruit_PCD8544(12, 11, 10, 9, 8);

const byte pompa = 3;
const byte dmuchawa = 4;
int tzadana = 29;
int tpompa = 27;
int temperatura;
byte ekran = 0;
byte zmiana = 0;
byte uruchomiony=0;
byte wygaszanie=0;

const byte ROWS = 4;
const byte COLS = 4;

char keys[ROWS][COLS] = {
  {'1', '2', '3', 'A'},
  {'4', '5', '6', 'B'},
  {'7', '8', '9', 'C'},
  {'*', '0', '#', 'D'}
};

byte rowPins[ROWS] = {0, 1, 2, 3};
byte colPins[COLS] = {4, 5, 6, 7};

int i2caddress = 0x20;

Keypad_I2C kpd = Keypad_I2C( makeKeymap(keys), rowPins, colPins, ROWS, COLS, i2caddress );

int odczytLiczba()
{
  return odczytCyfra() * 10 + odczytCyfra();
}

int odczytCyfra()
{
  switch (kpd.getKey())
  {
    case '0': return 0; break;
    case '1': return 1; break;
    case '2': return 2; break;
    case '3': return 3; break;
    case '4': return 4; break;
    case '5': return 5; break;
    case '6': return 6; break;
    case '7': return 7; break;
    case '8': return 8; break;
    case '9': return 9; break;
    default: odczytCyfra();
  }
}

void EkranStartowy()
{
  display.clearDisplay();
  display.setTextSize(1);
  display.setTextColor(BLACK);
  display.setCursor(13, 0);
  display.print("Sterownik");
  display.println();
  display.print("pieca CO v4.20");
  display.println();
  display.println();
  display.print("A-Temperatury");
  display.println();
  display.print("B-Ekran Stanu");
  display.println();
  display.print("C-Ust. pompy");
  display.display();
}

void EkranTemperatury ()
{
  display.clearDisplay();
  display.setTextSize(1);
  display.setTextColor(BLACK);
  display.setCursor(0, 0);
  sensors.requestTemperatures();
  display.println("Temp. pieca:");
  display.print(temperatura);
  display.print(" C");
  display.println();
  display.println("Temp. zadana:");
  if (zmiana == 1)
  {
    display.print("Edycja");
    display.display();
    tzadana = odczytLiczba();
    EEPROM.put(100, tzadana);
    zmiana = 0;
  }
  EEPROM.get(100, tzadana);
  display.print(tzadana);
  display.print(" C");
  display.println();
  display.display();
}

void EkranStanu()
{
  display.clearDisplay();
  display.setTextSize(1);
  display.setTextColor(BLACK);
  display.setCursor(0, 0);
  display.print("Stan systemu: ");
  display.println();
  display.print("Pompa: ");
  if (digitalRead(pompa) == 0)
  {
    display.println("WYL");
    display.display();
  } else display.println("WL");
  display.print("Dmuchawa:");
  if (digitalRead(dmuchawa) == 0)
  {
    display.println("WYL");
    display.display();
  } else display.println("WL");
  display.display();
}

void EkranPompa()
{
  display.clearDisplay();
  display.setTextSize(0.8);
  display.setTextColor(BLACK);
  display.setCursor(0, 0);
  display.println("Tem. wl. pompy");
  if (zmiana == 1)
  {
    display.print("Edycja");
    display.display();
    tpompa = odczytLiczba();
    EEPROM.put(0, tpompa);
    zmiana = 0;
  }
  EEPROM.get(0, tpompa);
  display.print(tpompa);
  display.print(" C");
  display.display();
}

void setup()
{
  display.begin();
  display.setContrast(60);
  EkranStartowy();
  Serial.begin(9600);
  sensors.begin();
  Wire.begin(); 
  kpd.begin();
  pinMode(pompa, OUTPUT);
  pinMode(dmuchawa, OUTPUT);
}

void loop() {
  temperatura=sensors.getTempCByIndex(0);
  char klawisz = kpd.getKey();
  
  switch (klawisz)
  {
    case 'A': ekran = 1; break;
    case 'B': ekran = 2; break;
    case 'C': ekran = 3; break;
    case '#': ekran = 4; break;
    default: NULL; break;
  }

  switch (ekran)
  {
    case 1: EkranTemperatury(); break;
    case 2: EkranStanu(); break;
    case 3: EkranPompa(); break;
    case 4: EkranStartowy(); break;
    default: NULL; break;
  }

  if (klawisz != NO_KEY) Serial.println(klawisz);

  if (klawisz == '*') zmiana = 1;
  
  if(klawisz == 'D') {
    wygaszanie=0;
    uruchomiony=0;
  }

  if(klawisz == '#') {
    sensors.requestTemperatures();
    int i = 0;
    float temperatureC = sensors.getTempCByIndex(i);
    Serial.print(" Temperatura: ");
    Serial.print(temperatureC);
    Serial.println(" °C");
  }

  if ((temperatura>=tzadana)||(wygaszanie==1)) digitalWrite(dmuchawa,LOW);
  else digitalWrite(dmuchawa,HIGH);
  
  if(temperatura>tpompa) {
    digitalWrite(pompa,HIGH);
    uruchomiony=1;
  } else digitalWrite(pompa,LOW);
  
  if((uruchomiony==1)&&(digitalRead(pompa)==0)) wygaszanie=1;

}

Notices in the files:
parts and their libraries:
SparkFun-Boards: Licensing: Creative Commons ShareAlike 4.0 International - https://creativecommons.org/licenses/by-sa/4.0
